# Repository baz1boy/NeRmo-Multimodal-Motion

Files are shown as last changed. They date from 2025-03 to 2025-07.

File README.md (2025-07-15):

# NeRmo Mouse Robot

Robot Simulation

The **video demonstration** shows here:



A 12-DOF legged small-sized quadruped robot capable of multi-modal motion modes. Different motion modes are tested in both simulation and real-world environments.

All files are configured based on the MuJoCo environment in Python, starting with the modeling and motion testing of a 2D planar leg and gradually progressing to the simulation of the entire robot, followed by real-world robotic testing.

## Features
- **12-DOF leg structure:** based on the tri-segemented linkage-based leg.
- **Multi-modal motion control:** including **basic motion**, **turning in place**, **self-recovery from falling**, **squeezing thourgh small openings**, and **surmounting obstacles**. The jump motion is also included but has not achieved effective performance.

## Setup
MuJoCo provides [Python bindings](https://mujoco.readthedocs.io/en/stable/python.html#python-bindings).

### Prerequisites
- Ubuntu 20.04/22.04
- Python 3.8+
- MuJoCo

### Simulation Configuraiton
The XML model files are stored in the `models` folder, with each leg individually modeled. In the main body XML file, all components—including the legs, head, body, tail, and environment are assembled. The model structures created in native **MJCF** format are replaced with CAD STL files located in the `meshes` folder. Ckeak the [modeling guide](https://mujoco.readthedocs.io/en/stable/modeling.html) and [reference manual](https://mujoco.readthedocs.io/en/stable/XMLreference.html) for understanding.

### Test Setup
Each motion test has a dedicated test script `sim_test_xxx.py`. In the scripts, it is important to ensure that the appropriate MuJoCo modeling environment files are imported. 

For certain tests, such as squeezing, which includes tests for **low-height openings** and **narrow-width openings**, make sure to modify the corresponding environment configuration in `robot_body_squeezing.xml` in `models` accordingly.

### Testing Scenario
`sim_test_turning.py`: The **turning test** marks the beginning of the turning in place testing. The preceding commented-out sections correspond to tests of twisting motion, including roll, pitch, and yaw rotations.

`sim_test_recover.py`: It includes the simulation of side-lying and back-lying postures, and unnecessary test cases need to be commented out.

`sim_test_squeezing.py`: It is used to test the robot's ability to pass through low-height and narrow-width openings. The testing target can be selected by commenting or uncommenting **"Through a low hole"** and **"Through a narrow hole"** accordingly. Depending on the selected target, the corresponding environment modeling—low test or narrow test—needs to be specified in `models/test environment/squeezing_scene.xml`.

`sim_test_lower_leaning.py`: In the **"Trajectory Points"** part, select the start and end positions of the foot end. Positions **1** to **4** correspond to lower posture testing, while **point 5** is used for **leaning posture testing**. The parameter **s** is used to adjust the **gait stride length** in the lower posture. Modify the height of passage in `models/test environment/move_scene.xml` to test the **minimum passable height** based on the body height data collected by the sensors when the robot operates in **lower posture** or **leaning posture**.

`sim_test_surmounting.py`: Adjust the obstacle dimension in `models/test environment/surmounting_scene.xml` to test the maximum surmountable height.

## Kinematics
All kinematics calculations follow the unit system used in MuJoCo, meaning that all lengths are measured in meters. The leg dimension data is read from `leg_Data.py`.

`leg_Joint.py` computes the **forward kinematics**, while `leg_IK.py` is used for **inverse kinematics** calculations. If errors occur during testing, it may be necessary to slightly adjust the value of `q_guess` to improve convergence.

## Control Architecture
In `sim_test_xxx.py`, the process always begins with initialization, transitioning the robot from the modeled position to the initial running posture `init_pleg`, and converting it to **servo control values** `q_init`.

### ControL Speed
The motion speed is adjusted by dividing a planned trajectory into `n_step` sets of control values. 

For example, for a motion defined by a start point and an end point, the value of `n_step` determines the motion speed along the trajectory between these two points, given that the step duration is fixed.

### Control Variables
Some control variables need to be modified in `sim_controller.py`, such as the step angle in the turning motion, rather than directly specifying the desired values in the test script.

The required leg control data for a motion is obtained from the **motion pattern library** in `body_posture.py`. The final optimization is then performed in **trajectory optimization** within `sim_controller.py`, where additional control for the head joints is also incorporated.

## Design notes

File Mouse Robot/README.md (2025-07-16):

# NeRmo Mouse Robot



A 12-DOF legged small-sized quadruped robot capable of multi-modal motion modes. Different motion modes are tested in both simulation and real-world environments.

All files are configured based on the MuJoCo environment in Python, starting with the modeling and motion testing of a 2D planar leg and gradually progressing to the simulation of the entire robot body, followed by real-world robotic testing.

## Features
- **12-DOF leg structure:** based on the tri-segemented linkage-based leg.
- **Multi-modal motion control:** including basic motion, turning in place, self-recovery from falling, squeezing thourgh small openings, and surmounting obstacles. The jump motion is also included but has not achieved effective performance.

## Setup
### Prerequisites
- Ubuntu 20.04/22.04
- Python 3.8+
- MuJoCo

### Simulation Configuraiton
The XML files are stored in the `models` folder, with each leg individually modeled. In the main body XML file, all components—including the legs, head, body, tail, and environment—are assembled. The model structures created in MuJoCo are replaced with CAD STL files located in the `meshes` folder.

### Test Setup
Each motion test has a dedicated test script `sim_test_xxx.py`. In the scripts, it is important to ensure that the appropriate MuJoCo modeling environment files are imported. 

For certain tests, such as **squeezing**, which includes tests for **low-height openings** and **narrow-width openings**, make sure to modify the corresponding environment configuration in `robot_body_squeezing.xml` in `models` accordingly.

## Kinematics
All kinematics calculations follow the unit system used in MuJoCo, meaning that all lengths are measured in **meters**. The leg **dimension data** is read from `leg_Data.py`.

`leg_Joint.py` computes the **forward kinematics**, while `leg_IK.py` is used for **inverse kinematics calculations**. If errors occur during testing, it may be necessary to slightly adjust the value of `q_guess` to improve convergence.

## Control Architecture
In `sim_test_xxx.py`, the process always begins with **initialization**, transitioning the robot from the modeled position to the initial running posture `init_pleg`, and converting it to **servo control values** `q_init`.

### ControL Speed
The motion speed is adjusted by dividing a planned trajectory into `n_step` sets of control values. 

For example, for a motion defined by a start point and an end point, the value of `n_step` determines the motion speed along the trajectory between these two points, given that the step duration is fixed.

### Control Variables
Some control variables need to be modified in `sim_controller.py`, such as the step angle in the **turning motion**, rather than directly specifying the desired values in the test script.

The required leg control data for a motion is obtained from the **motion pattern library** in `body_posture.py`. The final optimization is then performed in **trajectory optimization** within `sim_controller.py`, where additional control for the head joints is also incorporated.

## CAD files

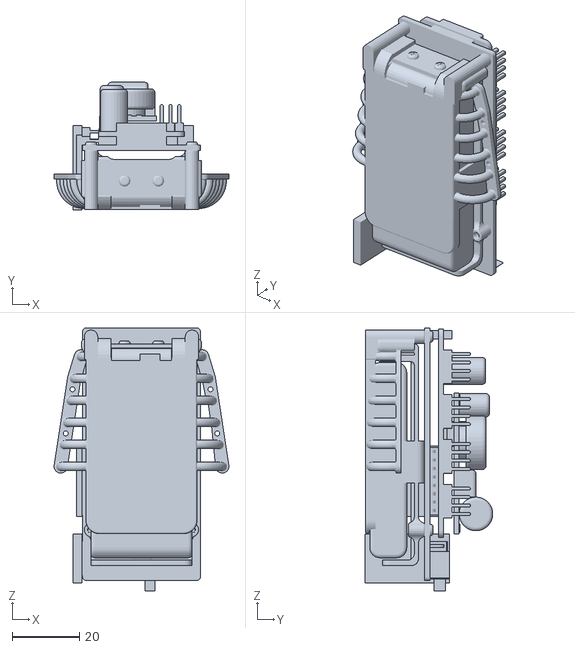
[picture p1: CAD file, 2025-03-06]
Mouse Robot/simRobot_Test/models_12DOF/body_assets/meshes/assembly_solar.stl
52.0 x 37.9 x 78.1

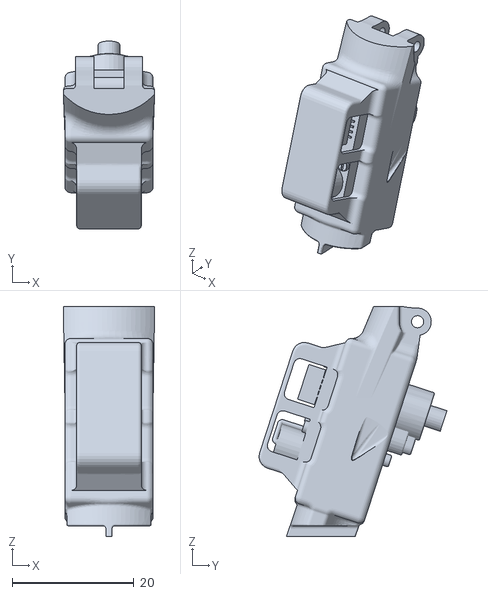
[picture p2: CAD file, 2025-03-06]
Mouse Robot/simRobot_Test/models_12DOF/body_assets/meshes/tail/tail_main.stl
15.0 x 30.8 x 37.8

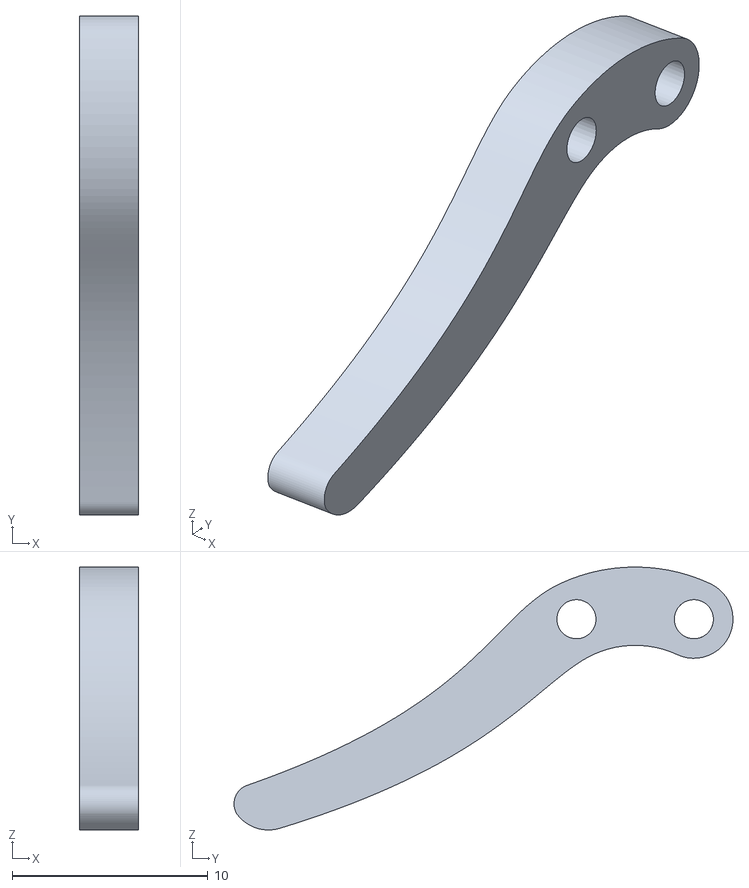
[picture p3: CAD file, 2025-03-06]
Mouse Robot/simLeg2D_Test/HindLeft_Leg/meshes/metatarsus_IHG.stl
3.00 x 25.5 x 13.4

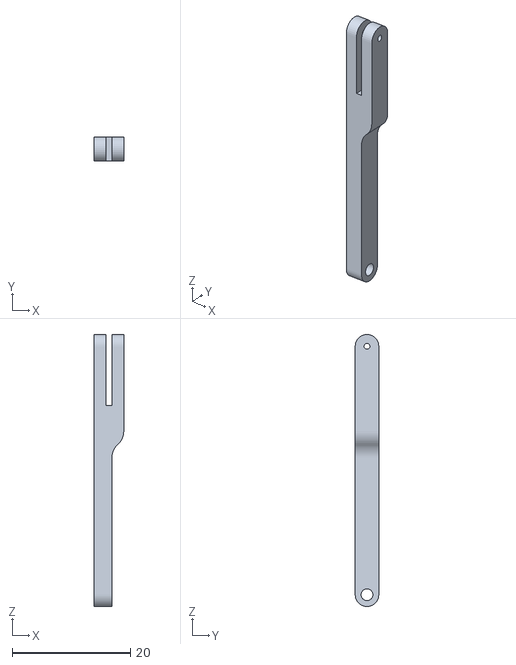
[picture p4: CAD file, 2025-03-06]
Mouse Robot/simLeg3D_Test/HindLeft_Leg/meshes/femur_CD.stl
5.00 x 4.00 x 46.0

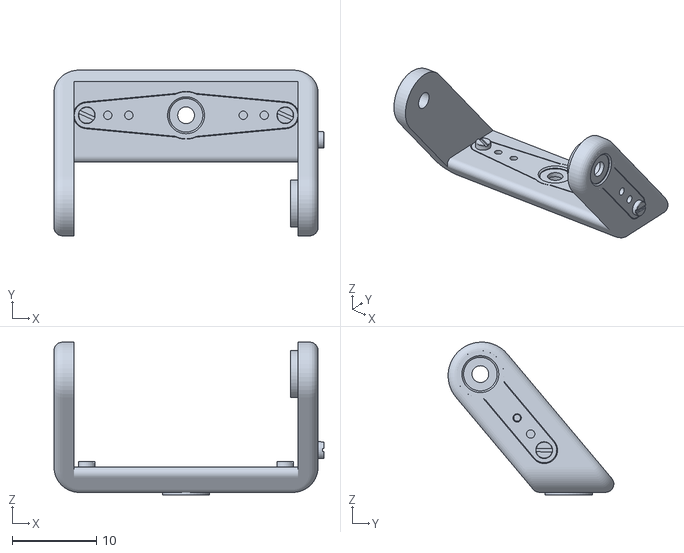
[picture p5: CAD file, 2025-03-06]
Mouse Robot/simRobot_Test/models/body_assets/meshes/head_bracket.stl
32.1 x 19.7 x 18.2

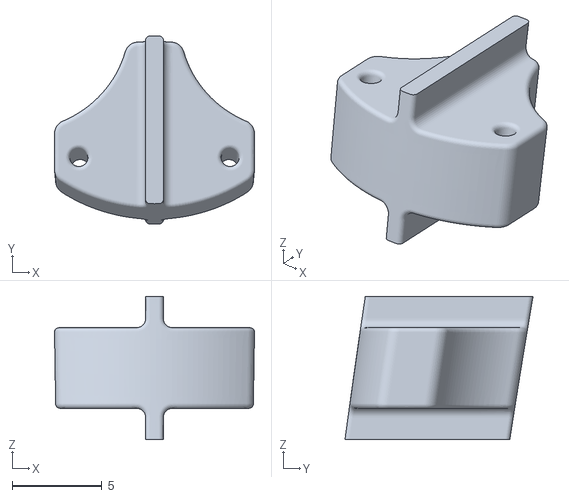
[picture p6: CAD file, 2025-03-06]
Mouse Robot/simRobot_Test/models/body_assets/meshes/tail/t11.stl
11.2 x 10.5 x 8.00

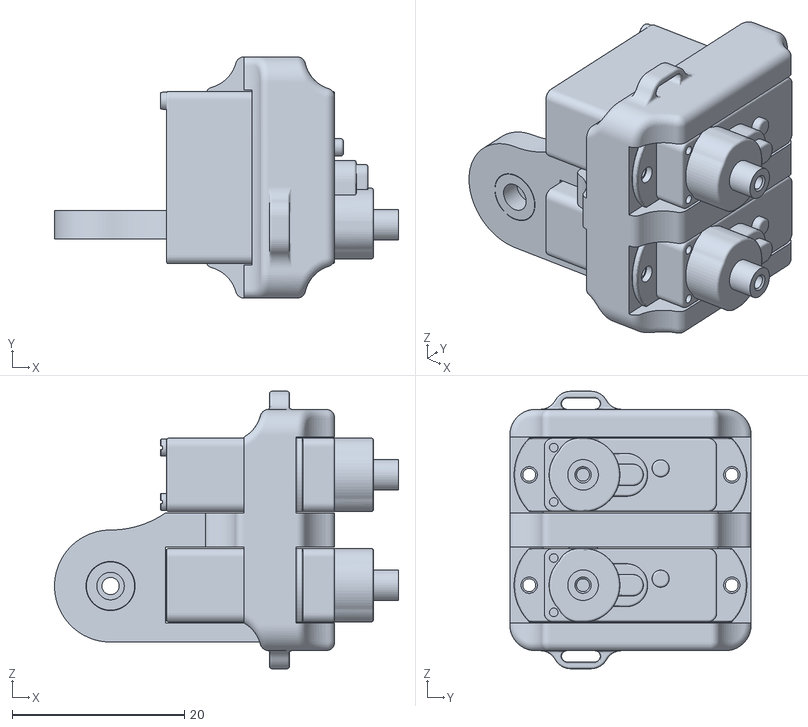
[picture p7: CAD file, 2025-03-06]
Mouse Robot/simRobot_Test/models/fore_left_assets/meshes/Shoulder_left.stl
39.9 x 28.0 x 32.2

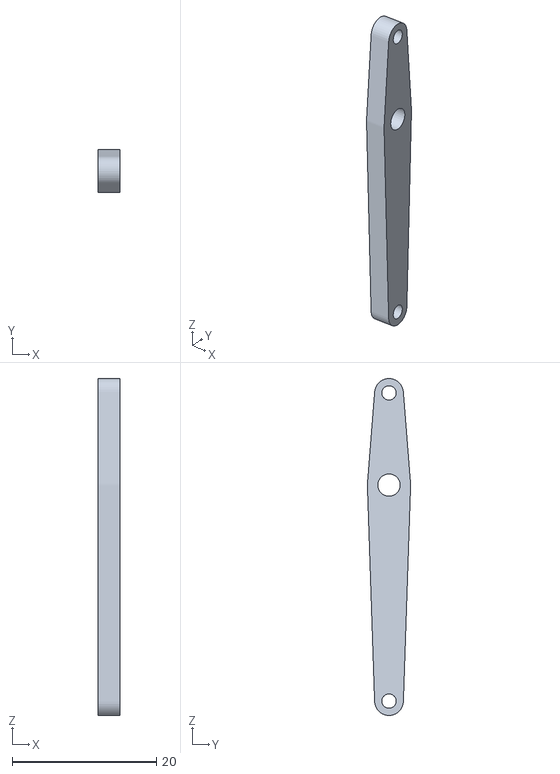
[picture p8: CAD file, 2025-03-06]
Mouse Robot/simRobot_Test/models/hind_left_assets/meshes/tibia_DEH.stl
3.00 x 6.00 x 46.8

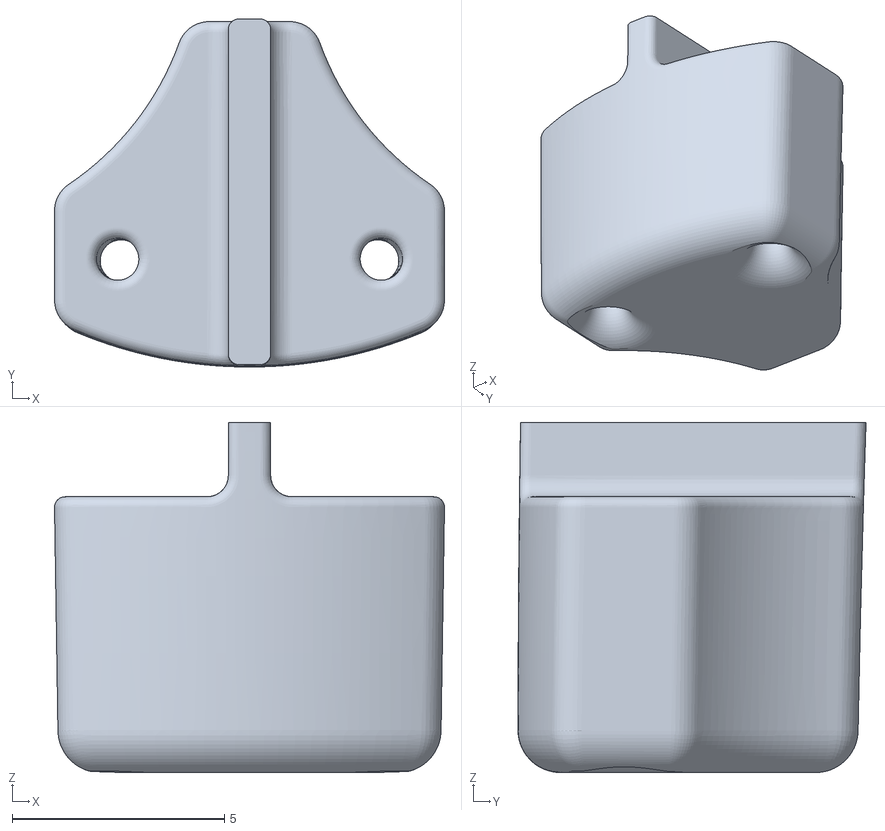
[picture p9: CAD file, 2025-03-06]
Mouse Robot/simRobot_Test/models_12DOF/body_assets/meshes/tail/t19.stl
9.19 x 8.20 x 8.25

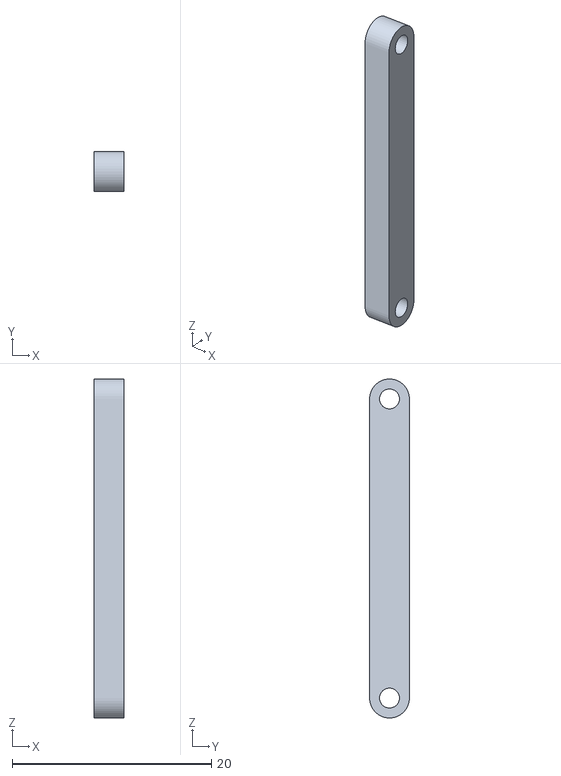
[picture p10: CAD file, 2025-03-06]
Mouse Robot/simRobot_Test/models_12DOF/fore_left_assets/meshes/tibia_FG.stl
3.00 x 4.00 x 34.0

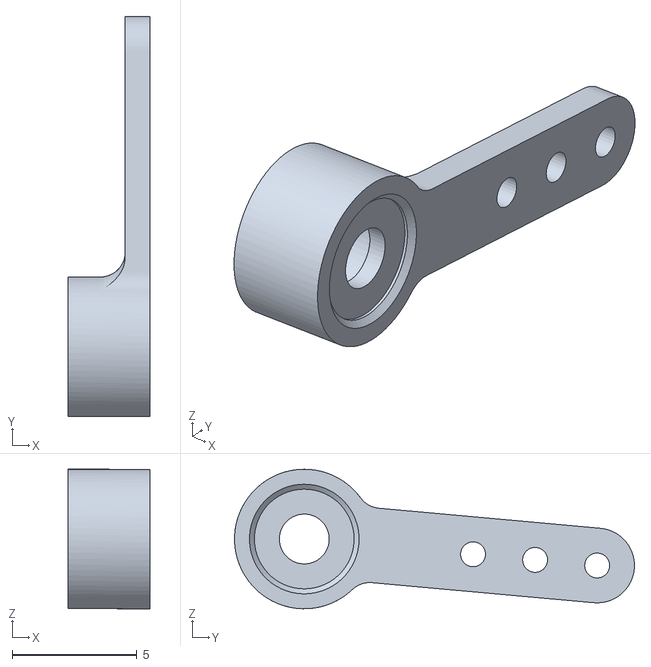
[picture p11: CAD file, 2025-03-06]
Mouse Robot/simRobot_Test/models_12DOF/fore_right_assets/meshes/Servo_Horn1_r.stl
3.30 x 16.1 x 5.60

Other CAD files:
Mouse Robot/simRobot_Test/models/hind_right_assets/meshes/metatarsus_IHG_r.stl
Mouse Robot/simRobot_Test/models_12DOF/hind_right_assets/meshes/Servo_Horn2_r.stl
Mouse Robot/simLeg2D_Test/HindLeft_Leg/meshes/Hip.stl
Mouse Robot/simLeg2D_Test/HindLeft_Leg/meshes/femur_AEF.stl
Mouse Robot/simLeg2D_Test/backup/body_assets/meshes/head_bracket.stl
Mouse Robot/simLeg2D_Test/backup/body_assets/meshes/spine.stl
Mouse Robot/simLeg2D_Test/backup/body_assets/meshes/tail/servo_horn_tail.stl
Mouse Robot/simLeg2D_Test/backup/body_assets/meshes/tail/t1.stl
Mouse Robot/simLeg2D_Test/backup/body_assets/meshes/tail/t10.stl
Mouse Robot/simLeg2D_Test/backup/body_assets/meshes/tail/t12.stl
Mouse Robot/simLeg2D_Test/backup/body_assets/meshes/tail/t13.stl
Mouse Robot/simLeg2D_Test/backup/body_assets/meshes/tail/t14.stl
Mouse Robot/simLeg2D_Test/backup/body_assets/meshes/tail/t15.stl
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

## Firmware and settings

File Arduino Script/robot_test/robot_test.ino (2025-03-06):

#include <ESP8266WiFi.h>
#include <WiFiUdp.h>
#include <Wire.h>
#include <Adafruit_PWMServoDriver.h>

// WiFi Setting
const char* SSID = "xxx";                    //  WiFi Name      
const char* PASSWORD = "xxxxxx";            //  WiFi Password

#define SCL 2  //IO_2 of ESP_01s connect the SCL of driver board
#define SDA 0  //IO_0 of ESP_01s connect the SDA of driver board
const int MPU = 0x68;

// UDP Setting
WiFiUDP Udp;
unsigned int localUdpPort = 6666;                 // choose a port addres
char incomingPacket[UDP_TX_PACKET_MAX_SIZE + 1];  // save the incoming UDP Packet
String ReplyBuffer = "got";

Adafruit_PWMServoDriver pwm = Adafruit_PWMServoDriver();  // default address 0x40

#define MOTOR_NUM 14   //Head12, LF 3 4 5, RF 6 7 8, LH 9 10 11, RH 12 13 14
#define PWM_Offset 0  // For Install, the start pin of motors, on board PCA9685
/*
 * DSM44 --> [0, 180]
 * Reference pulse duration: [0.5ms, 2.5ms] --> [0, 180]
 * 50Hz --> 20ms
 * SERVOMIN = 4096*0.5/20 = 102.4 --> 102
 * SERVOMAX = 4096*2.5/20 = 512
*/
int motorValues[MOTOR_NUM+1];
int curAngle[MOTOR_NUM];
bool goflag = false;

/**************************************Setup*****************************************/

void setup() {
  Serial.begin(115200);

  WiFi.begin(SSID, PASSWORD);
  while (WiFi.status() != WL_CONNECTED) {
    delay(500);
    Serial.print(".");
  }
  Udp.begin(localUdpPort);
  Serial.println("");
  Serial.println("WiFi connected");
  Serial.print("IP address: ");
  Serial.println(WiFi.localIP());
  Serial.printf("UDP server on port %d\n", localUdpPort);

  Wire.begin(SDA, SCL);
  /*
  Wire.beginTransmission(MPU);       // Start communication with MPU6050 // MPU=0x68
  Wire.write(0x6B);                  // Talk to the register 6B
  Wire.write(0x00);                  // Make reset - place a 0 into the 6B register
  Wire.endTransmission(true);        //end the transmission
  */
  pwm.begin();
  pwm.setPWMFreq(50);  // the maximum PWM frequency 60Hz

  for(int i = 0; i < MOTOR_NUM+1; i++){
    motorValues[i] = 0;
  } 
}

/************************************************************************************/

void loop() {
  int packetSize = Udp.parsePacket();
  if (packetSize) {
    int n = Udp.read(incomingPacket, UDP_TX_PACKET_MAX_SIZE);
    incomingPacket[n] = 0;

    Serial.print("Received packet: ");
    Serial.println(incomingPacket);
    streamSplit(incomingPacket, ",");

    Udp.beginPacket(Udp.remoteIP(), Udp.remotePort());
    Udp.write(ReplyBuffer.c_str());
    Udp.endPacket();

    goflag = true;

  } else {
    goflag = false;
  }

  if (goflag) {
    ctrlMotors();
  }
}

/***********************************************************************************/

void streamSplit(char* streamString, const char* flag) {
  int n = 0;
  char* result = NULL;

  result = strtok(streamString, flag);
  while (result != NULL) {
    String temp = String(result);
    motorValues[n++] = temp.toInt();
    result = strtok(NULL, flag);
  }

  for (int i = 0; i < MOTOR_NUM; i++) {
    curAngle[i] = motorValues[i];
    Serial.print(curAngle[i]);
    Serial.print(", ");
  }
  Serial.println("......");                                                                                                                                      
}

void ctrlMotors() {
  // *** left 0+, right 180-
  int pulse0 = map(curAngle[0]+90, 0, 180, 118, 510);       //Head rotation  turn left 90+, turn right 90-
  pwm.setPWM(0, 0, pulse0);
  
  int pulse1 = map(curAngle[1]+90, 0, 180, 100, 514);        //Head tilt up and down
  pwm.setPWM(1, 0, pulse1);

  int pulse2 = map(curAngle[2]+45, 0, 180, 105, 500);       //left fore leg servo1
  pwm.setPWM(2, 0, pulse2);
  int pulse3 = map(curAngle[3]-45, 0, 180, 130, 533);       //left fore leg servo2
  pwm.setPWM(3, 0, pulse3);
  int pulse4 = map(90-curAngle[4], 0, 180, 124, 524);       //left fore leg servo3
  pwm.setPWM(4, 0, pulse4);

  int pulse5 = map(135-curAngle[5], 0, 180, 128, 525);        //right fore leg servo1
  pwm.setPWM(5, 0, pulse5);
  int pulse6 = map(225-curAngle[6], 0, 180, 118, 520);        //right fore leg servo2
  pwm.setPWM(6, 0, pulse6);
  int pulse7 = map(curAngle[7]+90, 0, 180, 124, 532);       //right fore leg servo3
  pwm.setPWM(7, 0, pulse7);

  int pulse8 = map(curAngle[8]+45, 0, 180, 128, 532);        //left hind leg servo1
  pwm.setPWM(8, 0, pulse8);
  int pulse9 = map(curAngle[9]-45, 0, 180, 130, 536);        //left hind leg servo2
  pwm.setPWM(9, 0, pulse9);
  int pulse10 = map(90-curAngle[10], 0, 180, 118, 520);       //left hind leg servo3
  pwm.setPWM(10, 0, pulse10);

  int pulse11 = map(135-curAngle[11], 0, 180, 118, 510);        //right hind leg servo1
  pwm.setPWM(11, 0, pulse11);
  int pulse12 = map(225-curAngle[12], 0, 180, 111, 518);       //right hind leg servo2
  pwm.setPWM(12, 0, pulse12);
  int pulse13 = map(curAngle[13]+90, 0, 180, 107, 492);       //right hind leg servo3
  pwm.setPWM(13, 0, pulse13);

  //Serial.println("move");
}

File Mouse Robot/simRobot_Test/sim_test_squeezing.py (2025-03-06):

from matplotlib import pyplot as plt
from sim_control import simModel
from sim_controller import robotController, q2p, p2q
import numpy as np

INIT_STEPS = 2000
RUN_TIME_LENGTH = 20
SIM_STEPS = int(RUN_TIME_LENGTH/0.002)
if __name__ == '__main__':

	robot = simModel("models/robot_body_squeezing.xml")
	RC = robotController()
	T = 2
	timeStep = 0.002

	init_diff = RC.init_qdiff  	# due to model setup, modeling data
	pleg = RC.init_pleg
	pbody = RC.init_pbody
	angle = RC.init_angle
	center = RC.init_center
	step_diff = RC.stepDiff
	#print(stepdiff)

	## initialization
	q0 = np.array([0,0])
	q_init = RC.init_q
	q_init = np.hstack((q0,q_init))
	init_diff = np.hstack((q0,init_diff))
	#robot.ctrlViewer()

	t_init = 500
	q_phase = np.array([np.linspace(init_diff[i], q_init[i], int(t_init/2)) for i in range(14)]).T
	for i in range(t_init):
		if i<(t_init/2):
			ctrlData = np.radians(q_phase[i])
			robot.ctrlServo(ctrlData, timeStep)
		else:
			ctrlData = np.radians(q_phase[-1])
			robot.ctrlServo(ctrlData, timeStep)
		robot.ctrlViewer()
	
	### Trajectory Point
	p0 = np.array([[0.0325, 0.0039325, -0.05], [-0.0325, 0.0039325, -0.05], 
				 	[0.0325, 0.0039325, -0.05], [-0.0325, 0.0039325, -0.05]])
	p1 = np.array([[0.0325, -0.0160675, -0.05], [-0.0325, -0.0160675, -0.05], 
					[0.0325, -0.0160675, -0.05], [-0.0325, -0.0160675, -0.05]])		
	pm = (p0+p1)/2
	qm = p2q(pm)
	q_head = np.array([0,0])
	q_start = np.hstack((q_head, qm))

    ## Start up
	t_startup = 500
	q_startup = np.array([np.linspace(q_phase[-1][i], q_start[i], int(t_startup/2)) for i in range(14)]).T
	for i in range(t_startup):
		if i<(t_startup/2):
			ctrlData = np.radians(q_startup[i])
			robot.ctrlServo(ctrlData, timeStep)
		else:
			ctrlData = np.radians(q_startup[-1])
			robot.ctrlServo(ctrlData, timeStep)
		robot.ctrlViewer()
	pleg_cur = q2p(q_startup[-1])


	## Start Moving
	h_lift = 0.005
	q_move = RC.moveControl(p0, p1, h_lift)
	n = len(q_move)
	#print(q_move)
	#print(n)

	# ### Move Test
	# t_move = 6000
	# h_top = []
	# t_top = []
	# for i in range(t_move):
	# 	stepNUM = i % n
	# 	ctrlData = np.radians(q_move[stepNUM])
	# 	robot.ctrlServo(ctrlData, timeStep)
	# 	robot.ctrlViewer()
	# 	top = robot.topPosition()
	# 	#print(top)
	# 	h_top.append(top*1000)
	# 	t_top.append(i*0.002)

	# plt.plot(t_top, h_top, lw='2.5')
	# plt.title('Robot Height', fontsize=45)
	# plt.xlabel('Time(s)', fontsize=35)
	# plt.ylabel('Robot Top(mm)', fontsize=35)
	# plt.xticks(fontsize=30)
	# plt.yticks(fontsize=30)
	# #plt.legend(fontsize='large', loc='upper right', shadow=True, fancybox=True)
	# plt.show()

	t_transtion = 500
	q_transiton = np.array([np.linspace(q_startup[-1][i], q_move[0][i], int(t_transtion/2)) for i in range(14)]).T
	#print(q_transiton[0])
	for i in range(t_transtion):
		if i<(t_transtion/2):
			ctrlData = np.radians(q_transiton[i])
			robot.ctrlServo(ctrlData, timeStep)
		else:
			ctrlData = np.radians(q_transiton[-1])
			robot.ctrlServo(ctrlData, timeStep)
	
	### Squeezing Test
	t_move = 5000
	q_reach = np.zeros_like(q_transiton[-1])
	for i in range(t_move):
		stepNUM = i % n
		ctrlData = np.radians(q_move[stepNUM])
		robot.ctrlServo(ctrlData, timeStep)
		robot.ctrlViewer()
		top = robot.topPosition()
		#print(top)

		# hole detected:
		reach_door = robot.squeezingPosition()
		if(reach_door)<=0.04: #0.04
			q_reach = q_move[stepNUM]
			break

	t_pause = 200
	for i in range(t_pause):
		ctrlData = np.radians(q_reach)
		robot.ctrlServo(ctrlData, timeStep)
		robot.ctrlViewer()

	# bow head:
	# t_tran2squ = 500
	# q_squ1 = RC.squeezingControl(0)
	# q_tran2squ = np.array([np.linspace(q_reach[i], q_squ1[0][i], int(t_tran2squ/2)) for i in range(14)]).T
	# #print()
	# for i in range(t_tran2squ):
	# 	if i<(t_tran2squ/2):
	# 		ctrlData = np.radians(q_tran2squ[i])
	# 		robot.ctrlServo(ctrlData, timeStep)
	# 	else:
	# 		ctrlData = np.radians(q_tran2squ[-1])
	# 		robot.ctrlServo(ctrlData, timeStep)
	# 	robot.ctrlViewer()

	# t_squ1 = 5000
	# for i in range(t_squ1):
	# 	stepNUM = i % len(q_squ1)
	# 	ctrlData = np.radians(q_squ1[stepNUM])
	# 	robot.ctrlServo(ctrlData, timeStep)
	# 	robot.ctrlViewer()

	# 	# head passed:
	# 	reach_door = robot.squeezingPosition()
	# 	if(reach_door)<=-0.1:
	# 		q_passed_head = q_squ1[stepNUM]
	# 		step_passed_head = i
	# 		print(step_passed_head)
	# 		break

	# # crawling move:
	# h_top = []
	# t_top = []
	# q_squ2 = RC.squeezingControl(1)

	# t_1to2 = 400
	# q_1to2 = np.array([np.linspace(q_passed_head[i], q_squ2[0][i], int(t_1to2/2)) for i in range(14)]).T
	# for i in range(t_1to2):
	# 	if i<(t_1to2/2):
	# 		ctrlData = np.radians(q_1to2[i])
	# 		robot.ctrlServo(ctrlData, timeStep)
	# 	else:
	# 		ctrlData = np.radians(q_1to2[-1])
	# 		robot.ctrlServo(ctrlData, timeStep)
	# 	robot.ctrlViewer()

	# t_squ2 = 8000
	# for i in range(t_squ2):
	# 	stepNUM = i % len(q_squ2)
	# 	ctrlData = np.radians(q_squ2[stepNUM])
	# 	robot.ctrlServo(ctrlData, timeStep)
	# 	robot.ctrlViewer()
	# 	top = robot.spinePosition()
	# 	h_top.append(top*1000)
	# 	t_top.append(i*0.002)

	# 	# torso passed:
	# 	passed_torso = robot.holePosition()
	# 	if(passed_torso)<=0:
	# 		q_passed_torso = q_squ2[stepNUM]
	# 		step_passed_torso = i
	# 		print(step_passed_torso)
	# 		break

	# # motion traj adjust
	# q_squ3 = RC.squeezingControl(2)

	# t_2to3 = 200
	# q_2to3 = np.array([np.linspace(q_passed_torso[i], q_squ3[0][i], int(t_1to2/2)) for i in range(14)]).T
	# #print()
	# for i in range(t_2to3):
	# 	if i<(t_2to3/2):
	# 		ctrlData = np.radians(q_2to3[i])
	# 		robot.ctrlServo(ctrlData, timeStep)
	# 	else:
	# 		ctrlData = np.radians(q_2to3[-1])
	# 		robot.ctrlServo(ctrlData, timeStep)
	# 	robot.ctrlViewer()
	
	# t_squ3 = 2000
	# for i in range(t_squ3):
	# 	stepNUM = i % len(q_squ3)
	# 	ctrlData = np.radians(q_squ3[stepNUM])
	# 	robot.ctrlServo(ctrlData, timeStep)
	# 	robot.ctrlViewer()

	# plt.plot(t_top, h_top, lw='2.5')
	# plt.title('Robot Height', fontsize=45)
	# plt.xlabel('Time(s)', fontsize=35)
	# plt.ylabel('Robot Top(mm)', fontsize=35)
	# plt.xticks(fontsize=30)
	# plt.yticks(fontsize=30)
	# plt.legend(fontsize='large', loc='upper right', shadow=True, fancybox=True)
	# plt.show()
	
	"""
	Through a narrow hole
	"""
	# adjust posture
	t_adj1 = 500
	q_adj1 = RC.squeezingnarrowControl(0)

	q_nar1 = np.array([np.linspace(q_reach[i], q_adj1[i], int(t_adj1/2)) for i in range(14)]).T
	for i in range(t_adj1):
		if i<(t_adj1/2):
			ctrlData = np.radians(q_nar1[i])
			robot.ctrlServo(ctrlData, timeStep)
		else:
			ctrlData = np.radians(q_nar1[-1])
			robot.ctrlServo(ctrlData, timeStep)
		robot.ctrlViewer()

	q_adj2 = RC.squeezingnarrowControl(1)
	t_adj2 = len(q_adj2)
	for i in range(t_adj2+500):
		if i<(t_adj2):
			ctrlData = np.radians(q_adj2[i])
			robot.ctrlServo(ctrlData, timeStep)
		else:
			ctrlData = np.radians(q_adj2[-1])
			robot.ctrlServo(ctrlData, timeStep)
		robot.ctrlViewer()
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
